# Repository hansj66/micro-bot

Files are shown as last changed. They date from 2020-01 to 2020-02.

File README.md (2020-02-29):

# Micro:bit sumo robot
Firmware and hardware design files for the [TimeExpander.com](https://www.timeexpander.com/) Micro:bit based robot

The bot features two motor bridges, 3 x time of flight sensors, 4 x reflective object sensors and a GPIO Expander. 

Toolchain for building the firmware is the mBed online compiler.

You can watch one of the demo state machines in action here: https://youtu.be/_6B225iNg58

# Bill of materials
* 1 x Main PCB (https://github.com/hansj66/micro-bot/blob/master/Hardware/minisumo_v2.brd)
* 4 x line sensor PCBs (https://github.com/hansj66/micro-bot/blob/master/Hardware/minisumo_sensor.brd)
* 2 x Wheels (AliExpress)
* 2 x N20 motors (AliExpress)
* 2 x N20 motor bracket assembly (AliExpress)
* 3 x VL53L0X time of flight sensors on a carrier PCB (AliExpress)
* 1 x TCA9539 IO expander (Digikey)
* 1 x TXB0106PWR Bi-directional level translator  (Digikey)
* 4 x QRE1113GR Reflective optical sensors  (Digikey)
* 1 x 100uF aluminium capacitor
* 1 x 2x5 pin 2.54mm female header (Digikey)
* 1 x battery pack for 4x AAA  (Digikey)
* 1 x JS202011SCQN slide switch  (Digikey)
* 1 x SOT223 LM1117 3.3V regulator (Digikey)
* 1 x Mini caster assembly (AliExpress + 3D printed bracket)
* 2 x 3D printed spacers (between motors and PCB)
* 1 x 12 pin male breakaway header  (Digikey)
* 3 x 6 pin RA breakaway header  (Digikey)
* 1 x hook and loop tape (for attaching battery pack)
* 2 x 100nf capacitors (motor noise suppression)

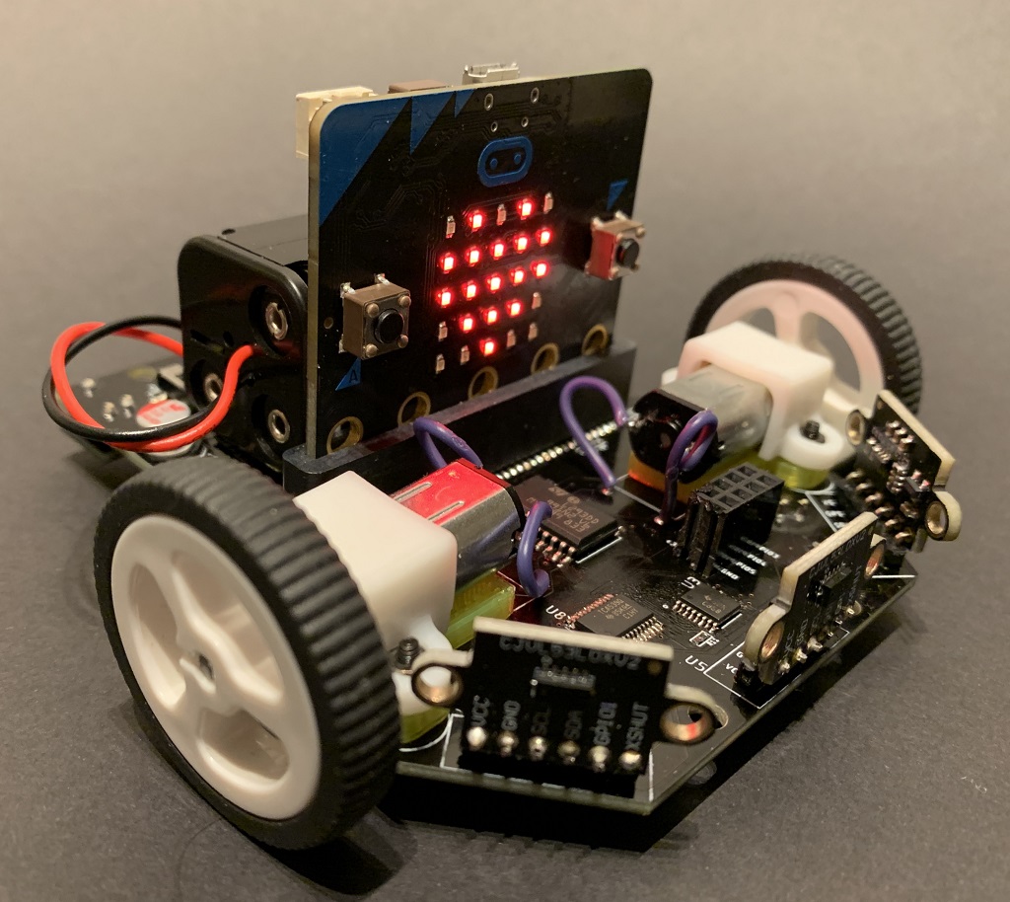
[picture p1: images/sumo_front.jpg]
Sumobot front


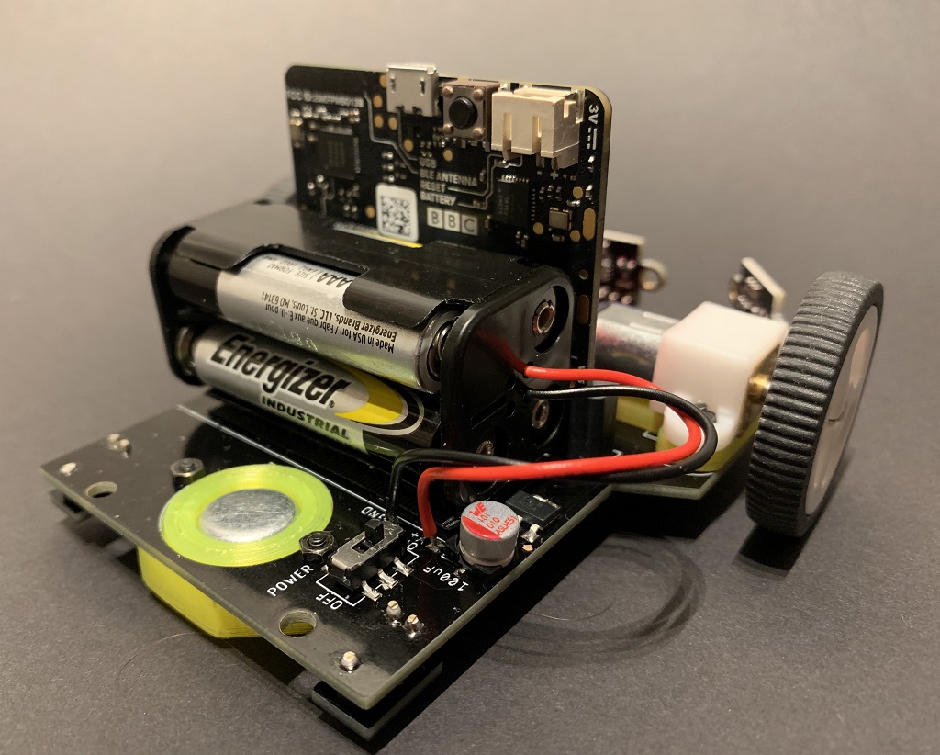
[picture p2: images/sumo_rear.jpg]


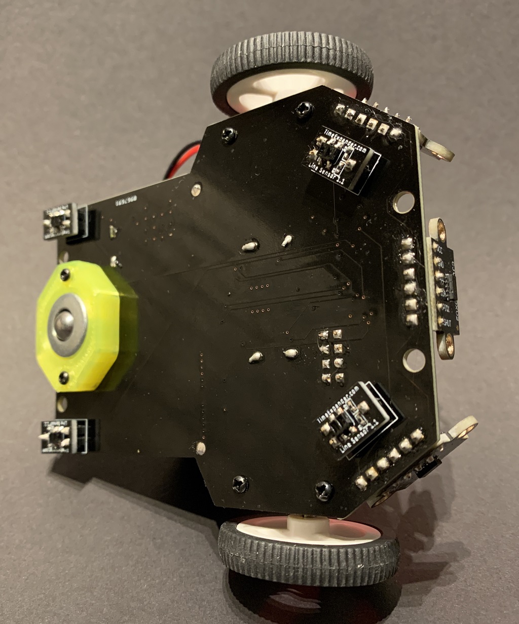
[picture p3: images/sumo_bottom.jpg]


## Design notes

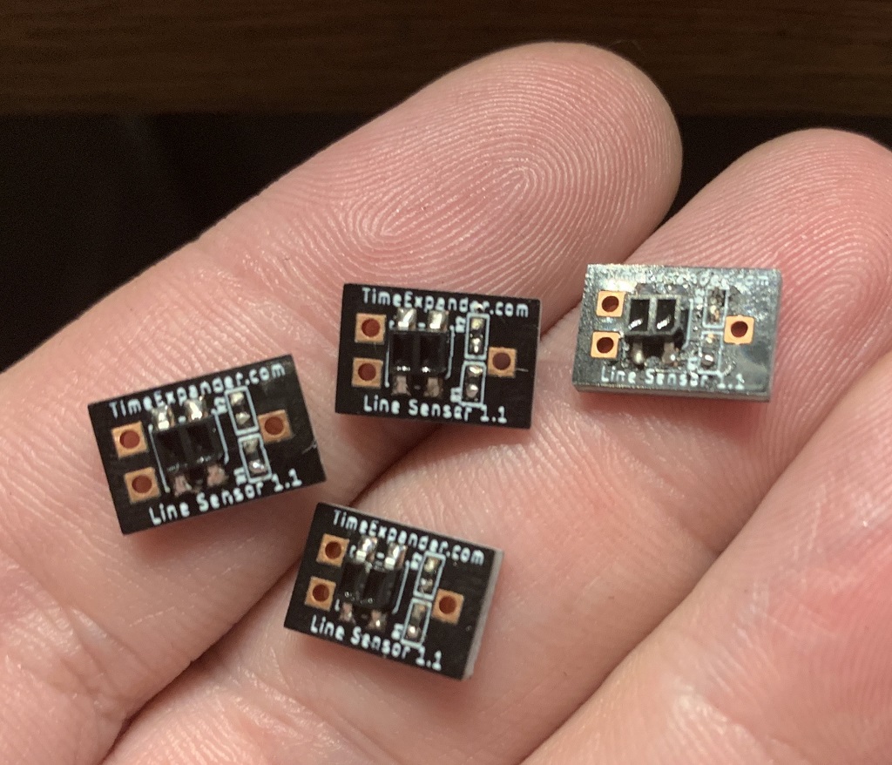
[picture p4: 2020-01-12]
images/sumo_sensors.jpeg

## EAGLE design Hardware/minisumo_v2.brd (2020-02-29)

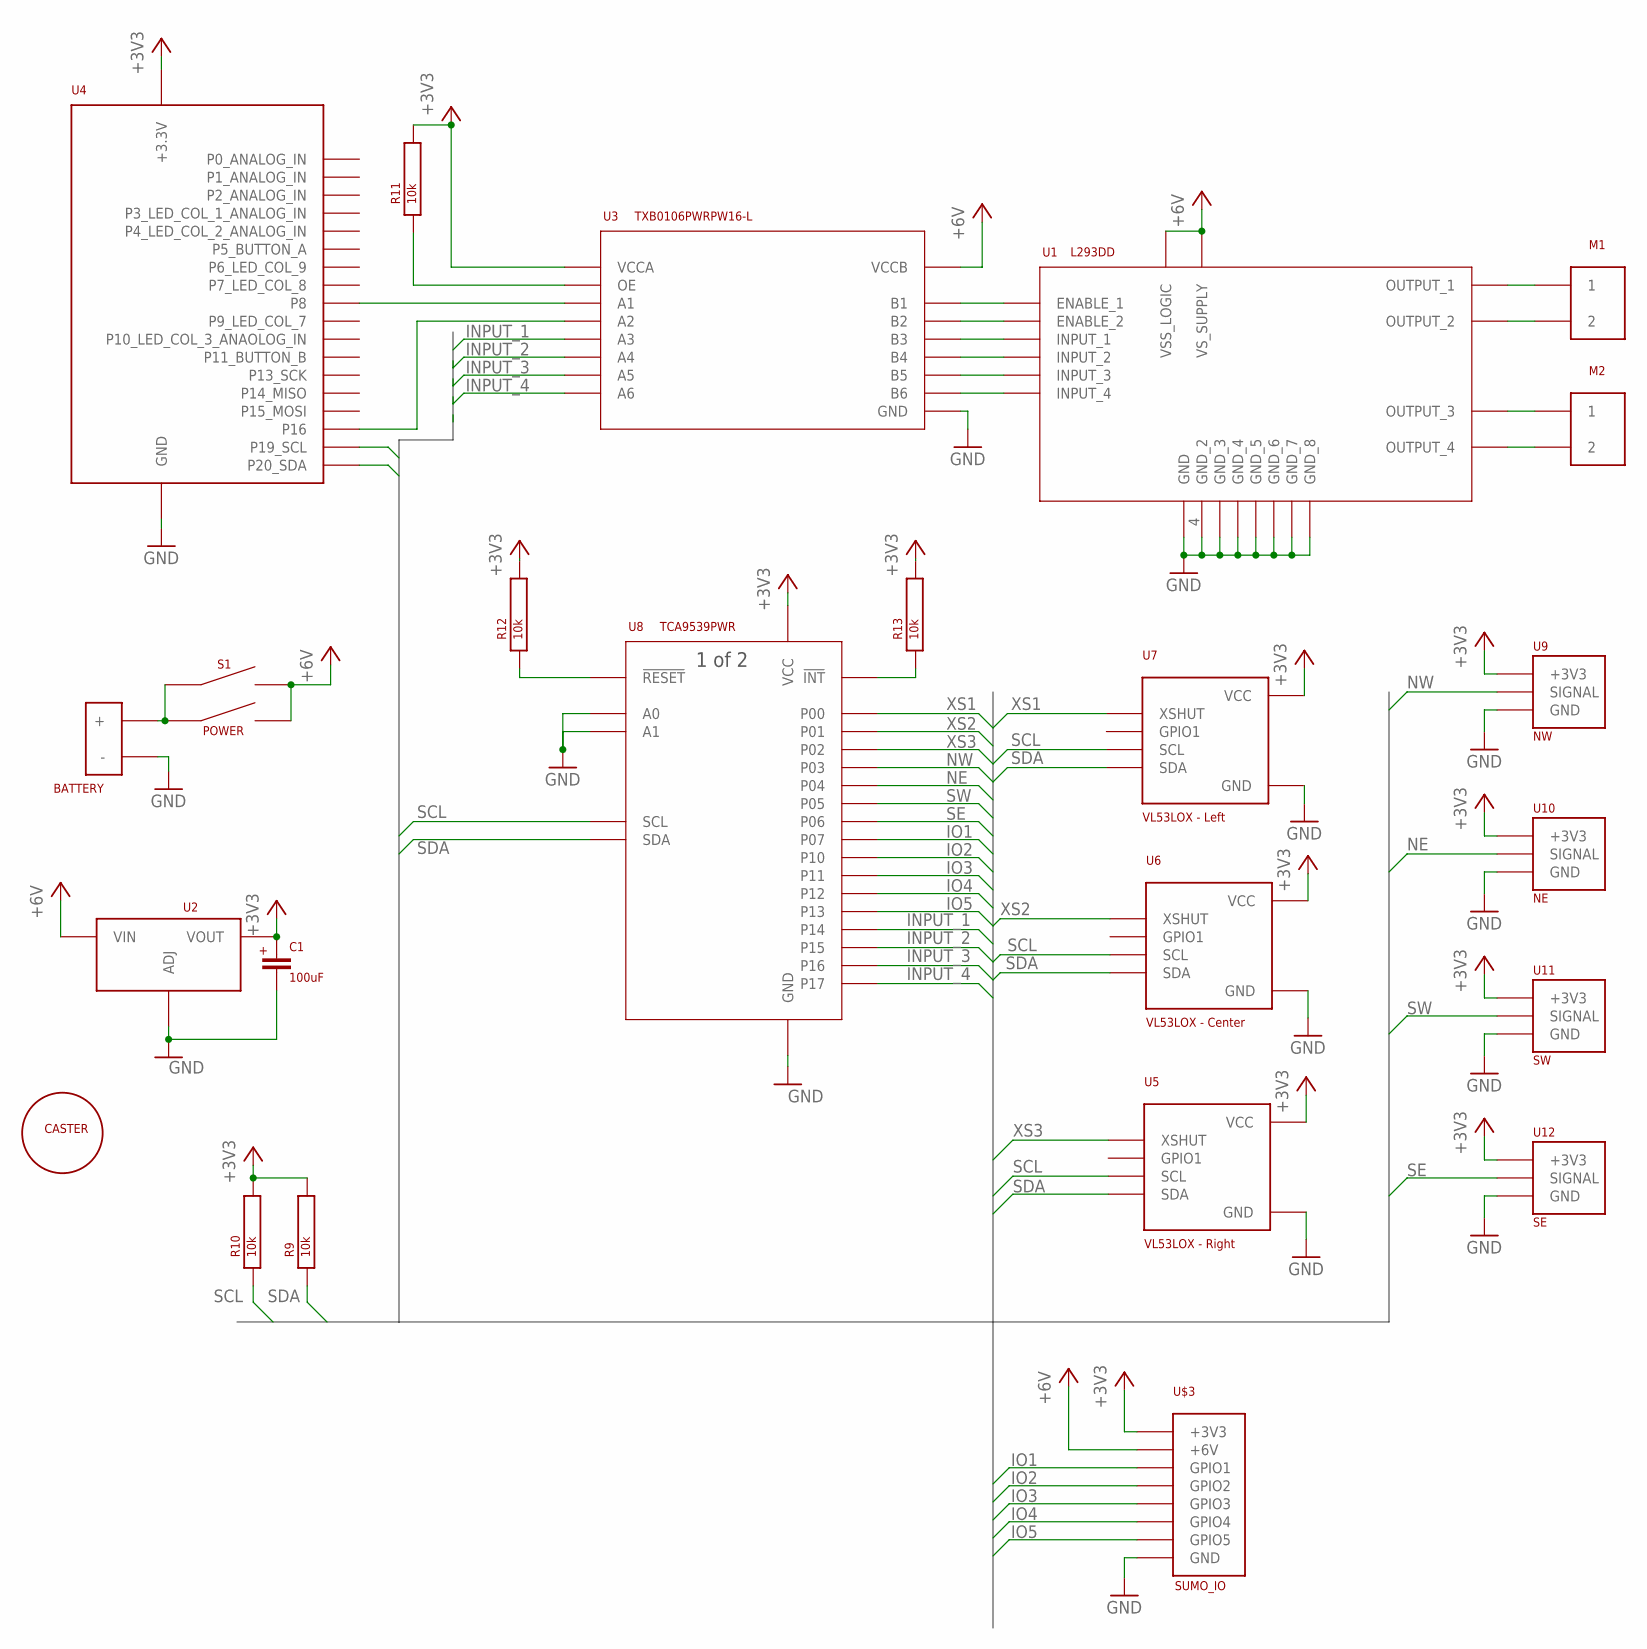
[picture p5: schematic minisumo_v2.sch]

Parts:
BATTERY: BATTERY_HOLDER_AAA_2X2
C1: 100uF; ALUMINUM_WURTH_100UF_865080243007
M1, M2: N20_MOTOR; N20-MOTOR-BRACKET
R9, R10, R11, R12, R13: 10k; RES_0402
S1: POWER; SWITCH_JS202011SCQN
U1: L293DD; SO-20
U2: LM1117; SOT-223
U3: TXB0106PWRPW16-L; PW16-L
U4: BBC Micro:bit; CYCLONE_MICROBIT_VERTICAL
U5: VL53LOX - Right; VL53LOX
U6: VL53LOX - Center; VL53LOX
U7: VL53LOX - Left; VL53LOX
U8: TCA9539PWR; 24-TSSOP
U9: NW; QRE1113_MODULE
U10: NE; QRE1113_MODULE
U11: SW; QRE1113_MODULE
U12: SE; QRE1113_MODULE
U$1: CASTER
U$3: SUMO_IO

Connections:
+3V3: C1.+, R9.P$2, R10.P$2, R11.P$2, R12.P$2, R13.P$2, U2.P$2 (VOUT), U2.VOUT$1 (VOUT), U3.2 (VCCA), U4.3.3V@9 (+3.3V), U4.3.3V@10 (+3.3V), U4.3.3V@11 (+3.3V), U4.3.3V@12 (+3.3V), U4.3.3V@13 (+3.3V), U4.3.3V@14 (+3.3V), U5.VCC, U6.VCC, U7.VCC, U8.24 (VCC), U9.+3V3, U10.+3V3, U11.+3V3, U12.+3V3, U$3.3V3 (+3V3)
+5V: S1.3 (B2), S1.6 (B1), U1.10 (VS_SUPPLY), U1.20 (VSS_LOGIC), U2.VIN, U3.15 (VCCB), U$3.6V (+6V)
GND: BATTERY.-, C1.-, U1.4 (GND_2), U1.5 (GND_3), U1.6 (GND_4), U1.7 (GND_5), U1.14 (GND_6), U1.15 (GND_7), U1.16 (GND_8), U1.17 (GND), U2.GND (ADJ), U3.9 (GND), U4.GND@1 (GND), U4.GND@2 (GND), U4.GND@3 (GND), U4.GND@4 (GND), U4.GND@5 (GND), U4.GND@6 (GND), U5.GND, U6.GND, U7.GND, U8.2 (A1), U8.12 (GND), U8.21 (A0), U9.GND, U10.GND, U11.GND, U12.GND, U$3.GND
INPUT_1: U3.4 (A3), U8.17 (P14)
INPUT_2: U3.5 (A4), U8.18 (P15)
INPUT_3: U3.6 (A5), U8.19 (P16)
INPUT_4: U3.7 (A6), U8.20 (P17)
IO1: U8.11 (P07), U$3.GPIO1
IO2: U8.13 (P10), U$3.GPIO2
IO3: U8.14 (P11), U$3.GPIO3
IO4: U8.15 (P12), U$3.GPIO4
IO5: U8.16 (P13), U$3.GPIO5
unnamed: U1.1 (ENABLE_1), U3.16 (B1)
unnamed: U1.11 (ENABLE_2), U3.14 (B2)
unnamed: U1.2 (INPUT_1), U3.13 (B3)
unnamed: U1.9 (INPUT_2), U3.12 (B4)
unnamed: M1.1, U1.3 (OUTPUT_1)
unnamed: M1.2, U1.8 (OUTPUT_2)
unnamed: M2.1, U1.13 (OUTPUT_3)
unnamed: M2.2, U1.18 (OUTPUT_4)
unnamed: U3.1 (A1), U4.P8
unnamed: U1.12 (INPUT_3), U3.11 (B5)
unnamed: U3.3 (A2), U4.P16
unnamed: U1.19 (INPUT_4), U3.10 (B6)
unnamed: BATTERY.+, S1.2 (A2), S1.5 (A1)
unnamed: R11.P$1, U3.8 (OE)
unnamed: R12.P$1, U8.3 (!RESET)
unnamed: R13.P$1, U8.1 (!INT)
NE: U8.8 (P04), U10.SIGNAL
NW: U8.7 (P03), U9.SIGNAL
SCL: R10.P$1, U4.P21_SCL (P19_SCL), U5.SCL, U6.SCL, U7.SCL, U8.22 (SCL)
SDA: R9.P$1, U4.P20_SDA, U5.SDA, U6.SDA, U7.SDA, U8.23 (SDA)
SE: U8.10 (P06), U12.SIGNAL
SW: U8.9 (P05), U11.SIGNAL
XS1: U7.XSHUT, U8.4 (P00)
XS2: U6.XSHUT, U8.5 (P01)
XS3: U5.XSHUT, U8.6 (P02)

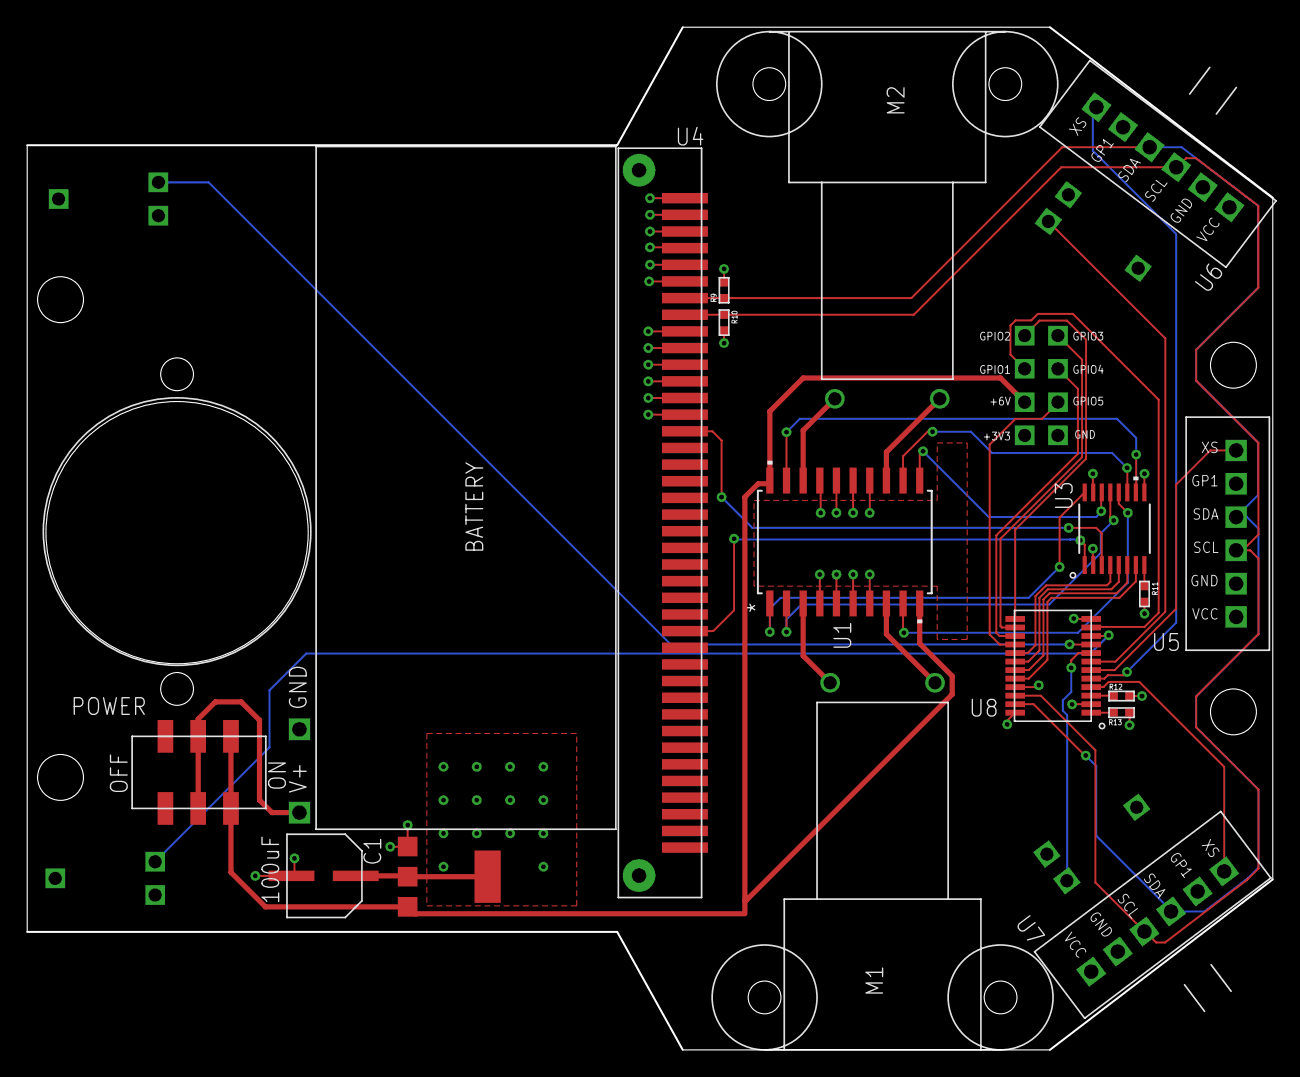
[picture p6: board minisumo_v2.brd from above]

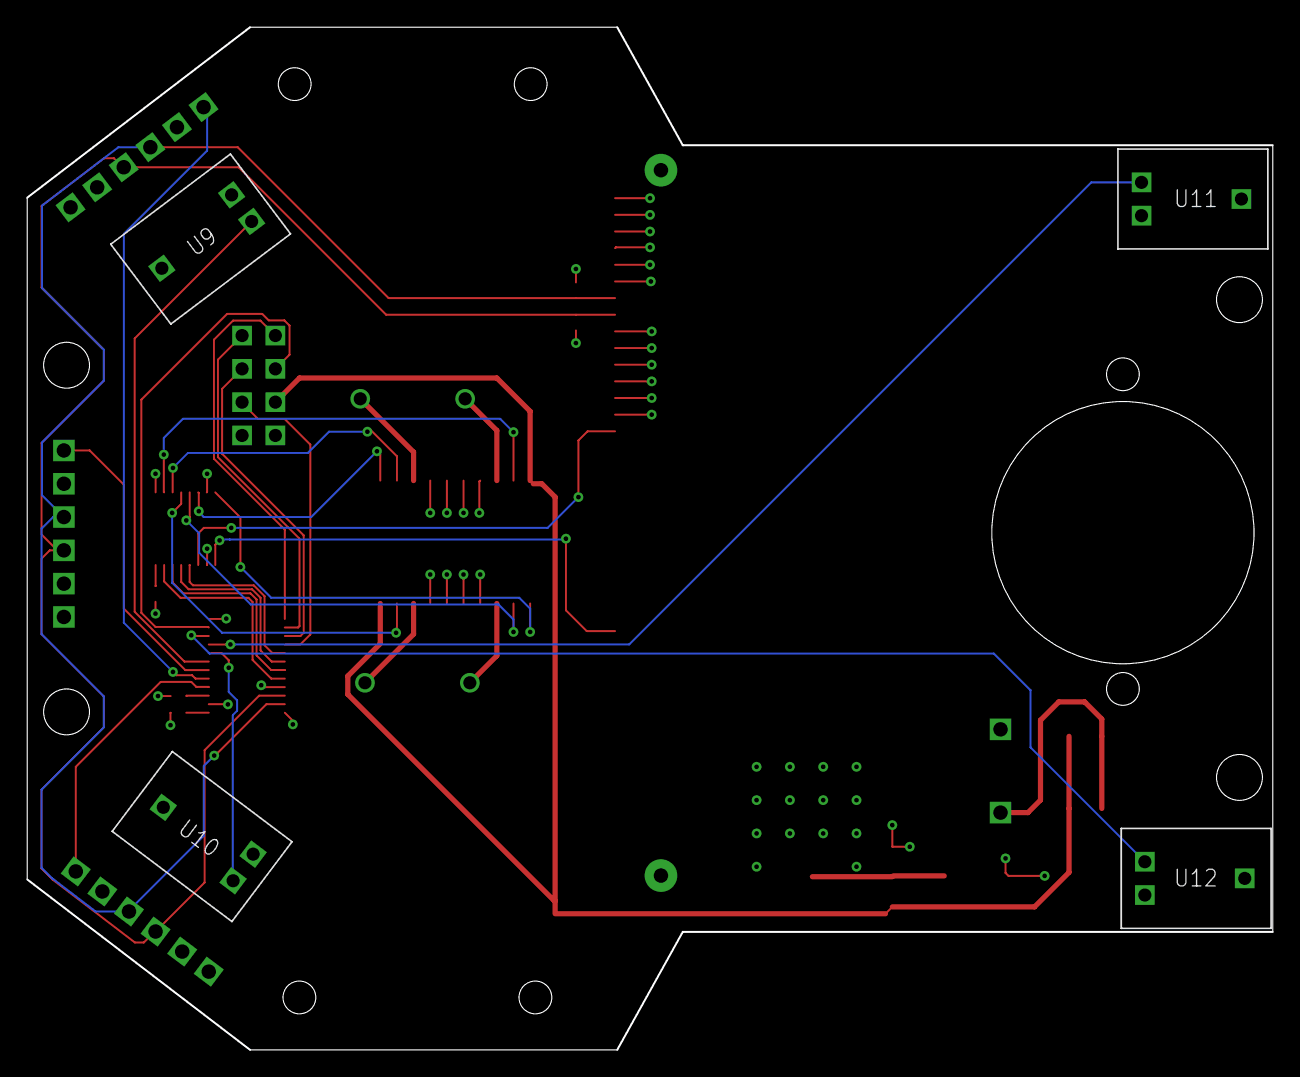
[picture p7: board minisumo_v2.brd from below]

Board: 4 copper layers, 95.0 x 78.0 mm, 24 parts (4 on the bottom side), 37 nets.

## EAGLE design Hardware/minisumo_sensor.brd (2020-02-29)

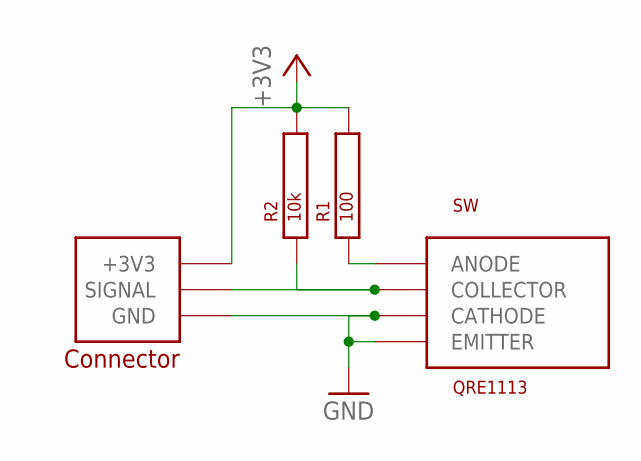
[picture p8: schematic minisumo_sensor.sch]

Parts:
R1: 100; RES_0402
R2: 10k; RES_0402
SW: QRE1113
U$1: QRE1113_CONNECTOR

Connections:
+3V3: R1.P$2, R2.P$2, U$1.+3V3
GND: SW.CATHODE, SW.EMITTER, U$1.GND
unnamed: R2.P$1, SW.COLLECTOR, U$1.SIGNAL
unnamed: R1.P$1, SW.ANODE

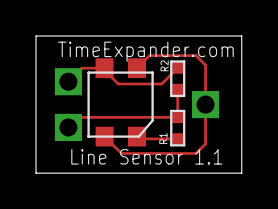
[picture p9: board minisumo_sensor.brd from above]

Board: 2 copper layers, 11.4 x 7.6 mm, 4 parts (0 on the bottom side), 4 nets.

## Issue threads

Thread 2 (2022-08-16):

BOM

samuk, 2022-08-16:
I was curious how much it would be to make these. I'm on Linux so Eagle is a pain. Could you provide a BOM please?

I can view the files and generate Gerbers but the BOM is empty for some reason?

samuk, 2022-09-06:
[minisumo_BOMv2.csv](https://github.com/hansj66/micro-bot/files/9498007/minisumo_BOMv2.csv)
[minisumo_bomv2.txt](https://github.com/hansj66/micro-bot/files/9498008/minisumo_bomv2.txt)

Managed to get Eagle running

Closed 2022-09-06.

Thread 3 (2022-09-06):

Encoder version?

samuk, 2022-09-06:
Would you be interested in doing a minor variation of this to have a hole next to the motor & input for encoders? https://www.aliexpress.com/item/32857563560.html

I think with an ESP32 flavoured Micro:Bit device this code would then run https://github.com/platisd/smartcar_shield/tree/master/src

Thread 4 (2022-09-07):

Replace TCA9539PWR with TCA9555PWR?

samuk, 2022-09-07:
Working on a [BOM ](https://docs.google.com/spreadsheets/d/16ljmmDqe1J7KlZV-EWnNo2i8vnV5bdKIFAJKv4D_IHI/edit#gid=2048989373)

[TCA9539PWR is $13](https://lcsc.com/product-detail/I-O-Expanders_Texas-Instruments-TCA9539PWR_C131972.html)
[TCA9555PWR is $3.6 ](https://lcsc.com/product-detail/I-O-Expanders_Texas-Instruments-TCA9555PWR_C465732.html)

They are both TSSOP-24 parts. Would the replacement work? There is a [comparison here](https://www.apogeeweb.net/compare/tca9539pwr-vs-tca9555pwr.html)

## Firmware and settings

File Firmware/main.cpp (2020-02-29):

/*
*  Copyright [2020] [Hans Jørgen Grimstad]
*  
*  Licensed under the Apache License, Version 2.0 (the "License");
*  you may not use this file except in compliance with the License.
*  You may obtain a copy of the License at
*  
*      http://www.apache.org/licenses/LICENSE-2.0
*  
*  Unless required by applicable law or agreed to in writing, software
*  distributed under the License is distributed on an "AS IS" BASIS,
*  WITHOUT WARRANTIES OR CONDITIONS OF ANY KIND, either express or implied.
*  See the License for the specific language governing permissions and
*  limitations under the License.
*/

#include "mbed.h"
#include "MicroBit.h"
#include "MicroBitDisplay.h"
#include "MicroBitButton.h"
#include "pinout.h"
#include "IOExpander.h"
#include "motor.h"
#include "proximity_sensor.h"
#include "line_sensor.h"
#include "platform.h"
#include "graphics.h"
#include "MicroBitPin.h"
#include "state_machine_line_follower.h"
#include "state_machine_sumo.h"

I2C i2c(I2C_SDA0, I2C_SCL0); 

MicroBitDisplay display;
IOExpander io;
ProximitySensorArray front_sensor(&io);
LineSensorArray bottom_sensor(&io);
Platform p(&io);
Motor motor(&io);

char logMessage[128];

MicroBitButton buttonA(MICROBIT_PIN_BUTTON_A, MICROBIT_ID_BUTTON_A, MICROBIT_BUTTON_ALL_EVENTS, PullUp);
MicroBitButton buttonB(MICROBIT_PIN_BUTTON_B, MICROBIT_ID_BUTTON_B, MICROBIT_BUTTON_ALL_EVENTS, PullUp);

int main() 
{
    wait_ms(1000);
    
    printf("-----------------------\n\r");
    printf("------ Micro:bot ------\n\r");
    printf("-----------------------\n\r");
    i2c.frequency(400000);

    wait_ms(2000);
    
    if (!p.SelfCheck()) {
        while (true)
        {
            DisplayFail();
        }
    }

    while (true)
    {
        DisplayReady();
        if ((buttonB.isPressed()) || (buttonA.isPressed()))
            break;
    }

    // LineFollower::Run();
    Sumo::Run();
}

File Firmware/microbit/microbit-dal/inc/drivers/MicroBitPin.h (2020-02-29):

/*
The MIT License (MIT)

Copyright (c) 2016 British Broadcasting Corporation.
This software is provided by Lancaster University by arrangement with the BBC.

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
THE SOFTWARE IS PROVIDED "AS IS", WITHOUT WARRANTY OF ANY KIND, EXPRESS OR
IMPLIED, INCLUDING BUT NOT LIMITED TO THE WARRANTIES OF MERCHANTABILITY,
FITNESS FOR A PARTICULAR PURPOSE AND NONINFRINGEMENT. IN NO EVENT SHALL
THE AUTHORS OR COPYRIGHT HOLDERS BE LIABLE FOR ANY CLAIM, DAMAGES OR OTHER
LIABILITY, WHETHER IN AN ACTION OF CONTRACT, TORT OR OTHERWISE, ARISING
FROM, OUT OF OR IN CONNECTION WITH THE SOFTWARE OR THE USE OR OTHER
DEALINGS IN THE SOFTWARE.
*/

#ifndef MICROBIT_PIN_H
#define MICROBIT_PIN_H

#include "mbed.h"
#include "MicroBitConfig.h"
#include "MicroBitComponent.h"
                                                        // Status Field flags...
#define IO_STATUS_DIGITAL_IN                0x01        // Pin is configured as a digital input, with no pull up.
#define IO_STATUS_DIGITAL_OUT               0x02        // Pin is configured as a digital output
#define IO_STATUS_ANALOG_IN                 0x04        // Pin is Analog in
#define IO_STATUS_ANALOG_OUT                0x08        // Pin is Analog out
#define IO_STATUS_TOUCH_IN                  0x10        // Pin is a makey-makey style touch sensor
#define IO_STATUS_EVENT_ON_EDGE             0x20        // Pin will generate events on pin change
#define IO_STATUS_EVENT_PULSE_ON_EDGE       0x40        // Pin will generate events on pin change

//#defines for each edge connector pin
#define MICROBIT_PIN_P0                     P0_3        //P0 is the left most pad (ANALOG/DIGITAL) used to be P0_3 on green board
#define MICROBIT_PIN_P1                     P0_2        //P1 is the middle pad (ANALOG/DIGITAL)
#define MICROBIT_PIN_P2                     P0_1        //P2 is the right most pad (ANALOG/DIGITAL) used to be P0_1 on green board
#define MICROBIT_PIN_P3                     P0_4        //COL1 (ANALOG/DIGITAL)
#define MICROBIT_PIN_P4                     P0_5        //COL2 (ANALOG/DIGITAL)
#define MICROBIT_PIN_P5                     P0_17       //BTN_A
#define MICROBIT_PIN_P6                     P0_12       //COL9
#define MICROBIT_PIN_P7                     P0_11       //COL8
#define MICROBIT_PIN_P8                     P0_18       //PIN 18
#define MICROBIT_PIN_P9                     P0_10       //COL7
#define MICROBIT_PIN_P10                    P0_6        //COL3 (ANALOG/DIGITAL)
#define MICROBIT_PIN_P11                    P0_26       //BTN_B
#define MICROBIT_PIN_P12                    P0_20       //PIN 20
#define MICROBIT_PIN_P13                    P0_23       //SCK
#define MICROBIT_PIN_P14                    P0_22       //MISO
#define MICROBIT_PIN_P15                    P0_21       //MOSI
#define MICROBIT_PIN_P16                    P0_16       //PIN 16
#define MICROBIT_PIN_P19                    P0_0        //SCL
#define MICROBIT_PIN_P20                    P0_30       //SDA

#define MICROBIT_PIN_MAX_OUTPUT             1023

#define MICROBIT_PIN_MAX_SERVO_RANGE        180
#define MICROBIT_PIN_DEFAULT_SERVO_RANGE    2000
#define MICROBIT_PIN_DEFAULT_SERVO_CENTER   1500

#define MICROBIT_PIN_EVENT_NONE             0
#define MICROBIT_PIN_EVENT_ON_EDGE          1
#define MICROBIT_PIN_EVENT_ON_PULSE         2
#define MICROBIT_PIN_EVENT_ON_TOUCH         3

#define MICROBIT_PIN_EVT_RISE               2
#define MICROBIT_PIN_EVT_FALL               3
#define MICROBIT_PIN_EVT_PULSE_HI           4
#define MICROBIT_PIN_EVT_PULSE_LO           5

/**
  * Pin capabilities enum.
  * Used to determine the capabilities of each Pin as some can only be digital, or can be both digital and analogue.
  */
enum PinCapability{
    PIN_CAPABILITY_DIGITAL = 0x01,
    PIN_CAPABILITY_ANALOG = 0x02,
    PIN_CAPABILITY_AD = PIN_CAPABILITY_DIGITAL | PIN_CAPABILITY_ANALOG,
    PIN_CAPABILITY_ALL = PIN_CAPABILITY_DIGITAL | PIN_CAPABILITY_ANALOG
};
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

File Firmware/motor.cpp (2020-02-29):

/*
*  Copyright [2020] [Hans Jørgen Grimstad]
*  
*  Licensed under the Apache License, Version 2.0 (the "License");
*  you may not use this file except in compliance with the License.
*  You may obtain a copy of the License at
*  
*      http://www.apache.org/licenses/LICENSE-2.0
*  
*  Unless required by applicable law or agreed to in writing, software
*  distributed under the License is distributed on an "AS IS" BASIS,
*  WITHOUT WARRANTIES OR CONDITIONS OF ANY KIND, either express or implied.
*  See the License for the specific language governing permissions and
*  limitations under the License.
*/

#include "mbed.h"
#include "motor.h"
#include "pinout.h"
#include "MicroBit.h"
#include "MicroBitPin.h"

// NOTE:
// 1)   Depending on the wiring of your motors, you may have to shuffle the
//      contents of the forward() reverse() and misc turn functions around
// 2)   The left and right throttle multiplier will have to be calibrated
//      for the bot to be able to move in a straight line over longer 
//      distances. 

MicroBitPin left(1, LEFT_SPEED, PIN_CAPABILITY_AD);
MicroBitPin right(2, RIGHT_SPEED, PIN_CAPABILITY_AD);

Motor::Motor(IOExpander * io) :
    _io(io),
    left_throttle_multiplier(1), 
    right_throttle_multiplier(1)
{
    left.setAnalogPeriodUs(10);
    left.setAnalogValue(500);
    right.setAnalogPeriodUs(10);
    right.setAnalogValue(500);
}

void Motor::test()
{
    left.setAnalogPeriod(1);
    left.setAnalogValue(500);
    right.setAnalogPeriod(1);
    right.setAnalogValue(500);
}

void Motor::forward()
{
    _io->set_value(LEFT_MOTOR_INPUT1, LOW);
    _io->set_value(LEFT_MOTOR_INPUT2, HIGH);
    _io->set_value(RIGHT_MOTOR_INPUT1, HIGH);
    _io->set_value(RIGHT_MOTOR_INPUT2, LOW);
}

void Motor::reverse() 
{
  _io->set_value(LEFT_MOTOR_INPUT1, HIGH);
  _io->set_value(LEFT_MOTOR_INPUT2, LOW);
  _io->set_value(RIGHT_MOTOR_INPUT1, LOW);
  _io->set_value(RIGHT_MOTOR_INPUT2, HIGH);
}

void Motor::turn_right()
{
  _io->set_value(LEFT_MOTOR_INPUT1, HIGH);
  _io->set_value(LEFT_MOTOR_INPUT2, LOW);
  _io->set_value(RIGHT_MOTOR_INPUT1, HIGH);
  _io->set_value(RIGHT_MOTOR_INPUT2, LOW);
}

void Motor::turn_left()
{
  _io->set_value(LEFT_MOTOR_INPUT1, LOW);
  _io->set_value(LEFT_MOTOR_INPUT2, HIGH);
  _io->set_value(RIGHT_MOTOR_INPUT1, LOW);
  _io->set_value(RIGHT_MOTOR_INPUT2, HIGH);
}

// SetSpeed changes the PWM duty cycle.
// Range 0-1023
void Motor::setSpeed(int speed)
{
    if (speed < 0)
        speed = 0;
    if (speed > 1023)
        speed = 1023;


    left.setAnalogValue((int)(speed*left_throttle_multiplier));
    right.setAnalogValue((int)(speed*right_throttle_multiplier));
}

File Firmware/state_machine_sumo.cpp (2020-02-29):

/*
*  Copyright [2020] [Hans Jørgen Grimstad]
*  
*  Licensed under the Apache License, Version 2.0 (the "License");
*  you may not use this file except in compliance with the License.
*  You may obtain a copy of the License at
*  
*      http://www.apache.org/licenses/LICENSE-2.0
*  
*  Unless required by applicable law or agreed to in writing, software
*  distributed under the License is distributed on an "AS IS" BASIS,
*  WITHOUT WARRANTIES OR CONDITIONS OF ANY KIND, either express or implied.
*  See the License for the specific language governing permissions and
*  limitations under the License.
*/

#include "mbed.h"
#include "state_machine_sumo.h"
#include "line_sensor.h"
#include "motor.h"
#include "proximity_sensor.h"

extern MicroBitDisplay display;
extern ProximitySensorArray front_sensor;
extern LineSensorArray bottom_sensor;
extern Motor motor;

namespace Sumo {
    
#define TARGET_CUTOFF 400
    
enum MESSAGE
{ 
    SCAN,
    TARGET_DETECT_FRONT,
    TARGET_DETECT_LEFT,
    TARGET_DETECT_RIGHT,
    NO_TARGET,
    FRONT_LINE_SENSOR_TRIGGERED,
    ERROR 
};

enum MESSAGE start_state(void)
{
    wait_ms(2000);
    return SCAN;
}

enum MESSAGE scan_state(void)
{
    printf("scan state\r\n");
    motor.setSpeed(200);
    motor.turn_right();
    while (true)
    {
        front_sensor.update();
        printf("Front sensor range: %d\r\n", front_sensor.centerRange());
        wait_ms(2);
        if (front_sensor.centerRange() < TARGET_CUTOFF)
        {
            return TARGET_DETECT_FRONT;
        }
    }

}
    
enum MESSAGE chase_state(void)
{
    printf("chase state\r\n");
    motor.forward();
    motor.setSpeed(700);
    while (true)
    {
        front_sensor.update();
        bottom_sensor.update();
        if ((LINE == bottom_sensor.NE) || (LINE == bottom_sensor.NW))
            return FRONT_LINE_SENSOR_TRIGGERED;

        if (front_sensor.centerRange() > TARGET_CUTOFF)
        {
            if (front_sensor.leftRange() < TARGET_CUTOFF)
                return TARGET_DETECT_LEFT;
            if (front_sensor.rightRange() < TARGET_CUTOFF)
                return TARGET_DETECT_RIGHT;
        }
    }
}

enum MESSAGE reverse_state(void)
{
    printf("reverse state\r\n");
    motor.reverse();
    motor.setSpeed(300);
    while (true) {
        if ((LINE == bottom_sensor.NE) || (LINE == bottom_sensor.NW))
        {
            wait_ms(1500);
            return SCAN;
        }

    }
}


enum MESSAGE align_right_state(void)
{
    printf("align right state\r\n");
    motor.setSpeed(200);
    motor.turn_right();
    while (true)
    {
        front_sensor.update();
        if (front_sensor.centerRange() < TARGET_CUTOFF)
        {
            return TARGET_DETECT_FRONT;
        }
    }

}

enum MESSAGE align_left_state(void)
{
    printf("align left state\r\n");
    motor.setSpeed(150);
    motor.turn_left();
    while (true)
    {
        front_sensor.update();
        if (front_sensor.centerRange() < TARGET_CUTOFF)
        {
            return TARGET_DETECT_FRONT;
        }
    }
}



enum STATE_ID 
{ 
    START_STATE = 0,
    SCAN_STATE, 
    CHASE_STATE,
    ALIGN_RIGHT_STATE,
    ALIGN_LEFT_STATE,
    REVERSE_STATE,
};

enum MESSAGE (*handler[])() = 
{
    start_state,
    scan_state,
    chase_state,
    align_right_state,
    align_left_state,
    reverse_state,
};


struct transition
{
    STATE_ID   current_state;
    MESSAGE message;
    STATE_ID    next_state;
};

#define TRANSITIONS 9

struct transition transitions[TRANSITIONS] = 
{
    {START_STATE, SCAN, SCAN_STATE},
    {SCAN_STATE, TARGET_DETECT_FRONT, CHASE_STATE},    
    {CHASE_STATE, NO_TARGET, SCAN_STATE},    
    {CHASE_STATE, TARGET_DETECT_RIGHT, ALIGN_RIGHT_STATE},    
    {ALIGN_RIGHT_STATE, TARGET_DETECT_FRONT, CHASE_STATE},    
    {CHASE_STATE, TARGET_DETECT_LEFT, ALIGN_LEFT_STATE},    
    {ALIGN_LEFT_STATE, TARGET_DETECT_FRONT, CHASE_STATE},    
    {CHASE_STATE, FRONT_LINE_SENSOR_TRIGGERED, REVERSE_STATE},    
    {REVERSE_STATE, SCAN, SCAN_STATE}
};




void Run()
{
    printf("Running state machine\r\n");
    
    display.print('H');

     enum STATE_ID current_state = START_STATE;
    enum MESSAGE message = SCAN;
    
    while (true) 
    {
        message = handler[current_state]();
        for (int i=0; i<TRANSITIONS; i++)
        {
            if ((transitions[i].current_state == current_state) && (transitions[i].message == message))
            {
                current_state = transitions[i].next_state;
                break;
            }
        }
    }
}

}

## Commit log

2020-01-12 Feature complete * using arduino framework
2020-02-12 Ported from arduino framework to mbed framework * Added harware selftest option on boot * Minor tweaks in Polulu VL53L0X library * Added a few visuals for the test sequence
2020-02-13 Added motor test
2020-02-29 Added hardware design files. * Moved the firmware to online mbed * Added two demo state machines
    [minisumo_sensor.brd, minisumo_sensor.sch, minisumo_v2.brd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]
2020-02-29 Removed comment regarding fixed issue
    [motor.cpp]
